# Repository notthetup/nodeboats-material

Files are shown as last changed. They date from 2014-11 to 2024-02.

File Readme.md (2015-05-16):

# NodeBoats Workshop


## Workshop Material

- [What to bring along?](instructions.md)
- [Workshop Introduction](presentation.md)
- [Getting Started](getting-started.md)
- [Ideas/Inspiration](ideas.md)
- [Competition Information](competition.md)
- [What to do if there's no Internet](no-internet.md)

### Aim

Let's Make something! Inspired by [NodeBoats at JSConf](http://makezine.com/2014/06/02/turning-coders-into-makers-at-jsconf-2014/)

Let's build boats that can be controlled by web technologies. We will make boats that can communicate over WiFi to a Node app.

The exact design of the boat and the control will be up to the individual team's creativity.

### Teams

- Maximum of 10 teams (that's all the kits we have)
- Each team has 2 members

### CampJS V 2015

**NodeBoats workshop at [CampJS V](http://v.campjs.com/)**

**Date** : 23-24th May 2015

**Venue** : Beach, Lord Somers Camp, Victoria, Australia

**Time** : 10am - 5pm *Catch the race on Sunday at TBA!*

### Competition

We will have a competition at the end of the day using the boats everyone created. The exact goal of the competition will be announced during the workshop.

The competition will be held at the **Beach at 5pm**

There will be prizes!

### Links

### History

*This workshop was first carried out at [JS Conf Asia 2014](http://2014.jsconf.asia/). Checkout the [Nodeboats Workshop Gallery](https://www.facebook.com/media/set/?set=a.615900415180712.1073741830.224477610989663&type=1).*

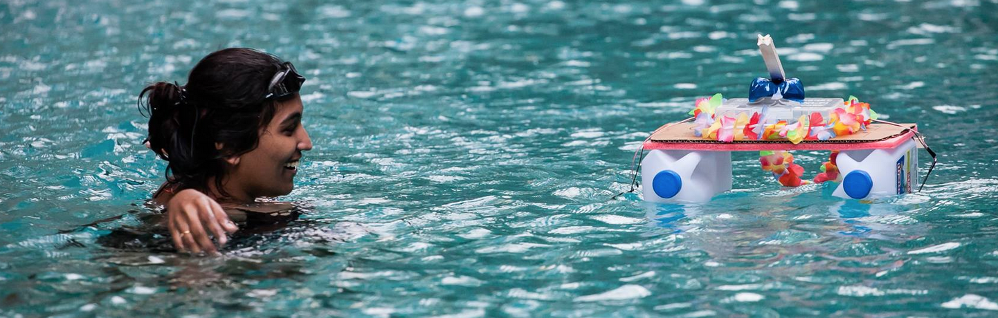
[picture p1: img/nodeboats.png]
Nodeboats workshop gallery (https://www.facebook.com/media/set/?set=a.615900415180712.1073741830.224477610989663&type=1)


#### JS Conf Asia 2014

**Nodeboat Builder workshop at [JSConf.Asia 2014](http://2014.jsconf.asia/)**

**Date** : 20th November 2014

**Venue** : Amara Sanctuary, Sentosa, Singapore

**Time** : 9.15am - 5:30pm *Catch the race at 5:15pm!*

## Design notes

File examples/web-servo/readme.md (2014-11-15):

#Rotate servo from the web

Using:

1. [Express](http://expressjs.com/)
- [Spark io](https://www.spark.io/)
- [Johnny Five](https://github.com/rwaldron/johnny-five)

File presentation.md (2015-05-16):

# NodeBoats Workshop!

# Material can be found in this github repo

**[bit.ly/nodeboatsworkshop](http://bit.ly/nodeboatsworkshop)**

# Grab your Kits
 - SparkCore Maker Kit
 - 1 Tamiya Submarine Motor
 - 1 Battery holder
 - 1 Pack of battries

# Hardware

We have a bunch of hardware, extra motors, tools and stuff. Help yourself, but don't be greedy!

# Get started with your Spark Core

- [Follow instructions here](getting-started.md)

# Get ready for the competition!

- [Competition information here](competition.md)
- Remember we're all here to share our <3 for JS and learn with each other. The competition is just for lulz.

# Let's work together and make some fricking robots!

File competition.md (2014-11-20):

# Competition.

## Time and Location

The competition will be held at the Dream Pool at Amara Sanctuary, at 5.15pm on 20th November 2014.

## Rules

1. All boats have to be controlled using remote control.
2. The boats have to complete the stipulated path as quickly as they can.
3. Any boat that sinks or drops something into (pollutes) the water will be disqualified.

## Competition Path

- Aim : Cross the dreamspool.
- Start : The wall nearest to the JSConf venue.
- End : The wall furthest from the JSConf venue.
- Metrics : How long you take to cross. Fastest wins!
- Tip : The waterfall on the side causes a constant water current towards the left.
- If your boat gets stuck or looses connection, we'll retrieve it for you and start over.

## Time Slots

1. Red Martians
2. The Sinking Barge
3. Superhero
4. RedMart Shark Boat
5. The JLT pearl
6. Cthulu
7. MeijiJS
8. Joosh Boat
9. NodeShip
10. Milky Way
11. Astuti

## Judging Criteria

| Criteria | Percentage | Notes |
| --- | --- | --- |
| Boat Design | 33.3333% | |
| Controller Design | 33.3333% | |
| Speed | 33.3333% | _Vrooooommm_ |
| Coin Toss | 0.0001% | _for Math_ |

## Prizes

1. [Hexy](http://arcbotics.com/products/hexy/)
2. [Sparki](http://arcbotics.com/products/sparki/)
3. [Raspberry Pi + Sparkfun Robot Board](https://www.sparkfun.com/products/11561)

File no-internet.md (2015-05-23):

# NodeBoats without Internet access

The current NodeBoats design uses [Spark Cloud](http://docs.particle.io/core/api/) to know the IP Address of the Spark Core. This IP Address is then used to communicate with the Spark Core.

So while, technically all the control communication happens locally, the initial step needs internet access.

In case of situations where internet access is flaky or inexistant, [MDNS](http://en.wikipedia.org/wiki/Multicast_DNS) can be used to exchange the IP Address based on a __HostName__.

## Setting up the SparkCore for MDNS

### Notes

- Unfortunately, the SparkCore tends to be flaky without a good connection to the SparkCloud, and can end trying to connect and not accepting any TCP messages.

- However, the Spark Core has a __SEMI_AUTOMATIC__ mode which allows it to run without a connection to Spark Cloud.

- Running the Spark Core in the __SEMI_AUTOMATIC__ will means none of the Spark APIs are accessible on the Spark Core or vice-versa.

- Hence, using the MDNS version of the SparkCore firmware, you won't be able to use the original version of `spark-io` or Spark APIs.

- You will have to __turn off your firewall__ to allow MDNS to work.

### Steps

1. Open the [Particle Build IDE](https://build.particle.io/build/#code).
2. Create a new App.
3. Copy and paste the firmware code from the [MDNS version of VoodooSpark](https://github.com/notthetup/voodoospark/blob/master/firmware/voodoospark.cpp) into the Build IDE.
4. Change the `CoreUID` to a unqiue string.
	```
	#define CoreUID "myPirateShip"
	```
5. Open the [Libraries Tab](https://build.particle.io/build/#libraries) in the Build IDE.
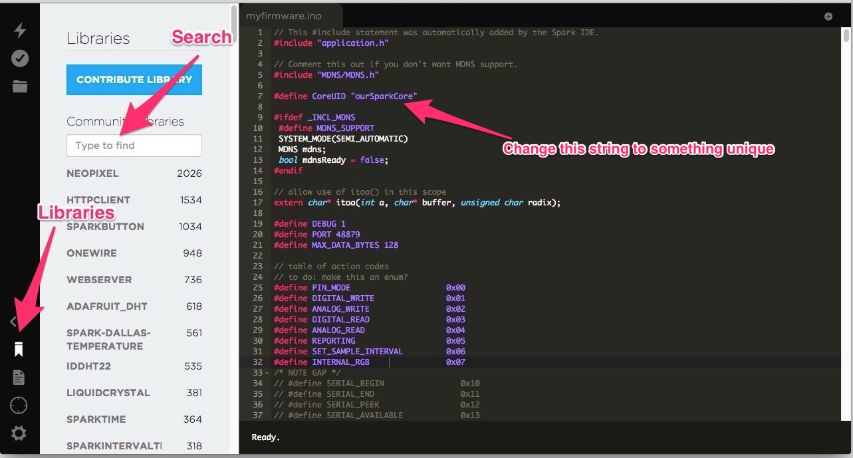
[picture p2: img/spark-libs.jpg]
spark libraries
	
6. Search for the [MDNS library](https://github.com/mrhornsby/spark-core-mdns).
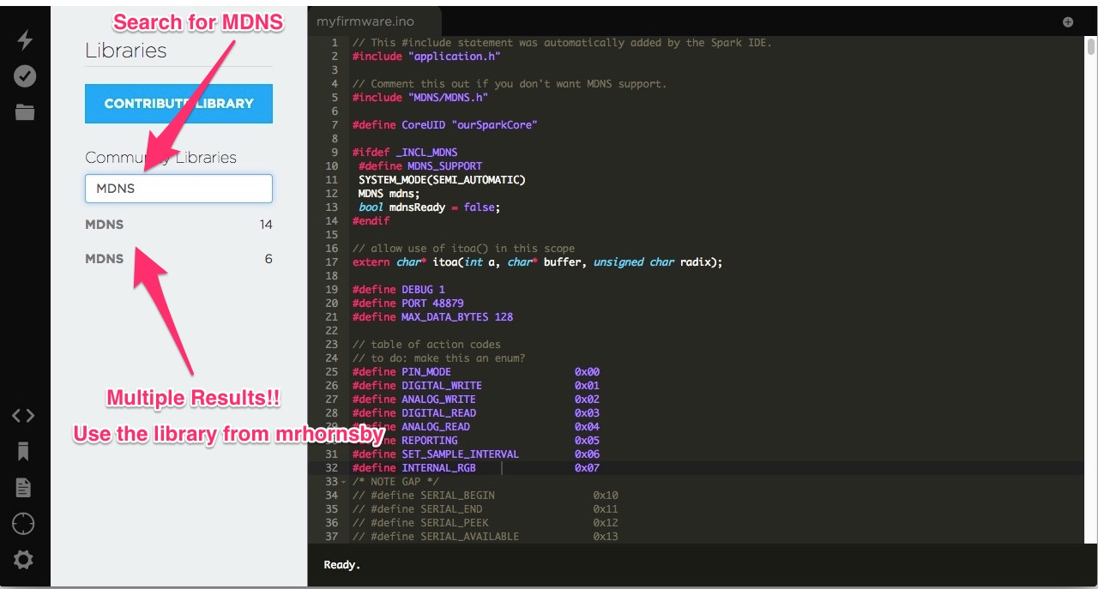
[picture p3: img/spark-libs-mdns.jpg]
spark libraries
	
7. Add the MDNS library to your new App.
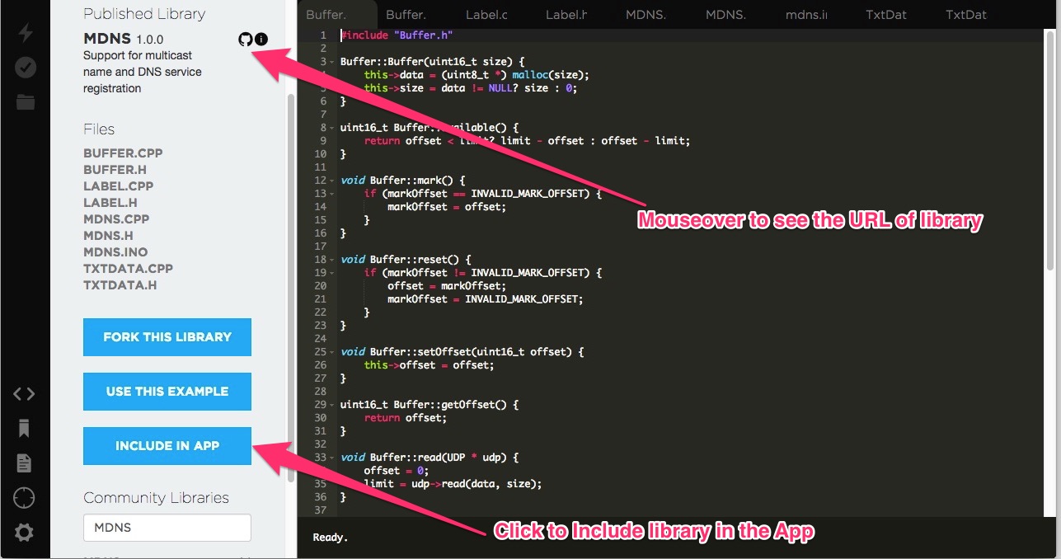
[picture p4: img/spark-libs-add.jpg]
spark libraries
	
8. Flash the new Firmware onto your SparkCore.

## Setting up the Spark-io for MDNS

- This [fork of Spark-io](https://github.com/notthetup/spark-io) supports MDNS.
- You might have to remove the original version of `spark-io`.
- You can install this using npm and the git url

	```shell
	npm i notthetup/spark-io
	```
- The MDNS version of `spark-io` works exactly the same, but tries to look for MDNS messages if a parameter called `hostname` is passed to the option Object in the constructor of `Spark`.

	```js
	var board = new five.Board({
	io: new Spark({
		hostname:'myPirateShip',
		deviceId:'{DEVICE_ID}',
		token:'{ACCESS_TOKEN}'
	})
});
	```

## Restoring Spark Core to original firmware.

### Notes

- Since the MDNS version of the firmware doesn't connect to Spark Cloud, re-flashing from the [Build IDE](https://build.particle.io/build/) will not work.
- To re-flash any other firmware, it easier to [first flash Tinker](https://github.com/spark/particle-cli#flashing-a-known-app) using dfu mode and then flash a new Firmware from the [Build IDE](https://build.particle.io/build/).

### Steps

1. Connect the Spark Core to USB.
2. Put the Spark Core in [dfu mode](http://docs.particle.io/core/modes/#core-modes-dfu-mode-device-firmware-upgrade).
3. Flash in Tinker using the `particle-cli` command

	```shell
	particle flash --usb tinker
	```
4. Wait for the Spark Core to be breathing cyan again before using it normally.

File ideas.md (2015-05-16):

# NodeBoats Twitter

[@nodeboats](https://twitter.com/nodeboats)

# NodeBoats at JSConf US

[Turning Coders into Makers](http://makezine.com/2014/06/02/turning-coders-into-makers-at-jsconf-2014/)

## Videos from JSCon US

[NodeBoats at JSConf 2014](https://www.youtube.com/watch?v=247MTokODOA)

[NodeBoats at JSConf2014](https://www.youtube.com/watch?v=eKqwo-jvRYo)

[Little ship nodeboat](https://www.youtube.com/watch?v=Kn9UaVDxHW8)

[Big nodeboat destroyer pirate ship](https://www.youtube.com/watch?v=zC0doS9-XZk)

[Look Ma! No Hands!](http://instagram.com/p/vXDkZywojq/)

## Videos from JSConf Asia

[NodeBoats at JSConf Asia 2014](https://www.youtube.com/watch?v=enCPdL7UnMw)

[NodeBoats Test](https://www.youtube.com/watch?v=YeJFM1E-l0o)

## Videos from RobotsConf

[NodeBoats Disaster!](https://www.youtube.com/watch?v=sJV63CuJXhQ)

[NodeBoat PaddleBoat Design](https://www.youtube.com/watch?t=10&v=A5_zRe0FQhk)

# Boat Design Ideas

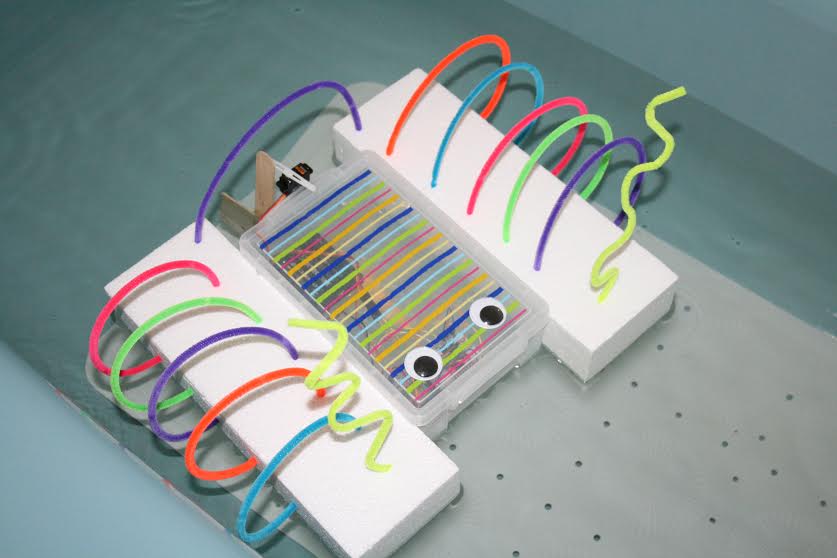
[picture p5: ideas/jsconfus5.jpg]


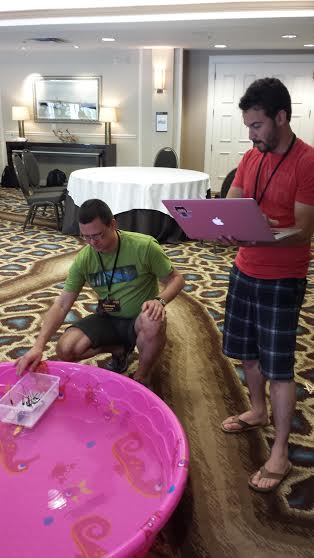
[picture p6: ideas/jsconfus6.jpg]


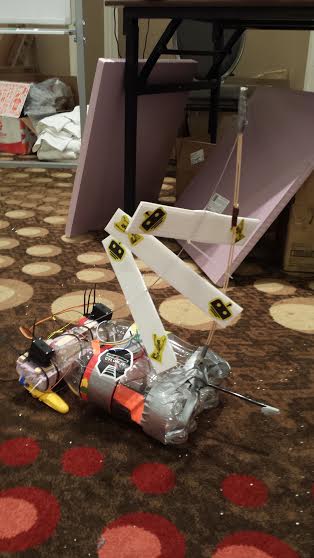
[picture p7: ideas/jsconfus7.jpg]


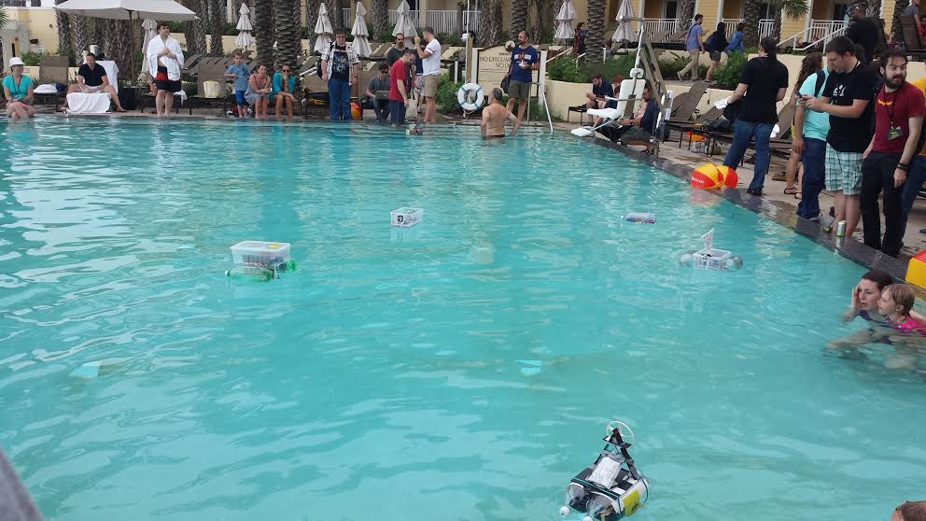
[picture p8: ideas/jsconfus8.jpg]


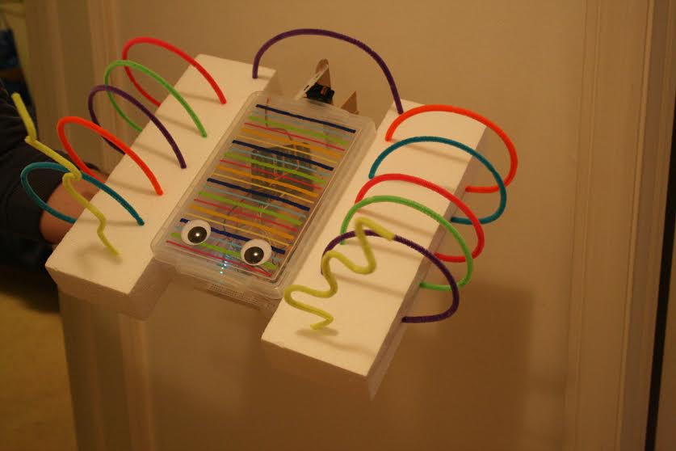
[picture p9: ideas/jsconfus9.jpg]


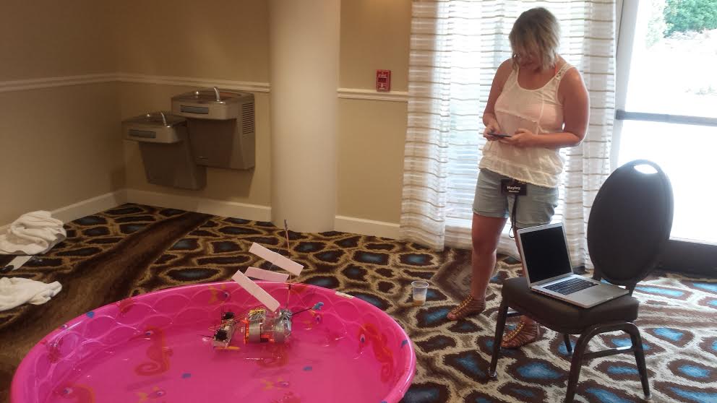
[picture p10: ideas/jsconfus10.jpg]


# Hacking the Tamiya Submarine Motor

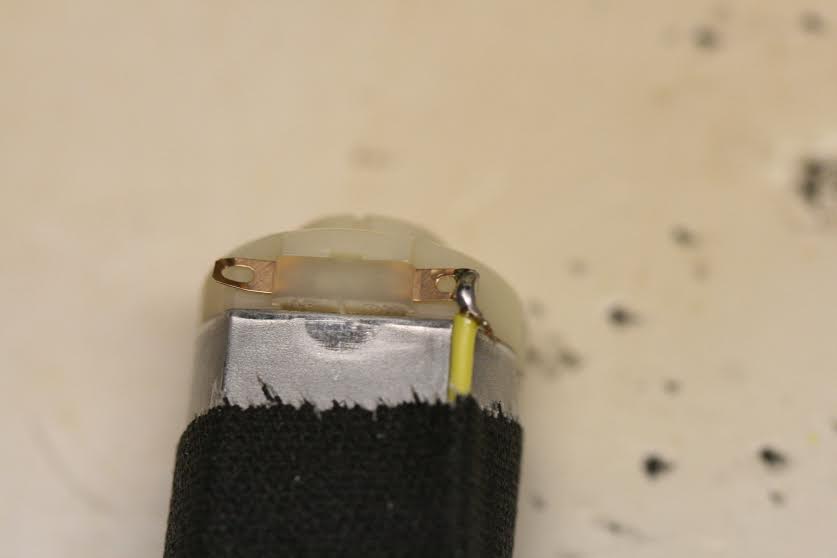
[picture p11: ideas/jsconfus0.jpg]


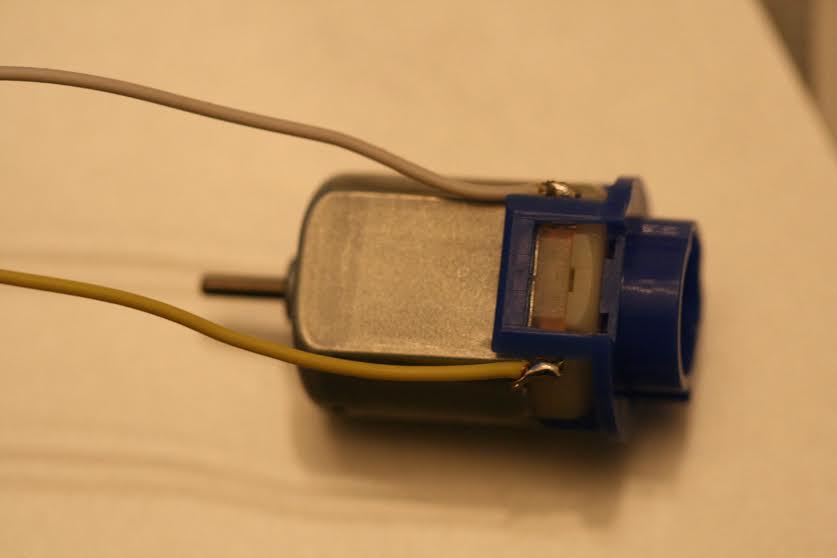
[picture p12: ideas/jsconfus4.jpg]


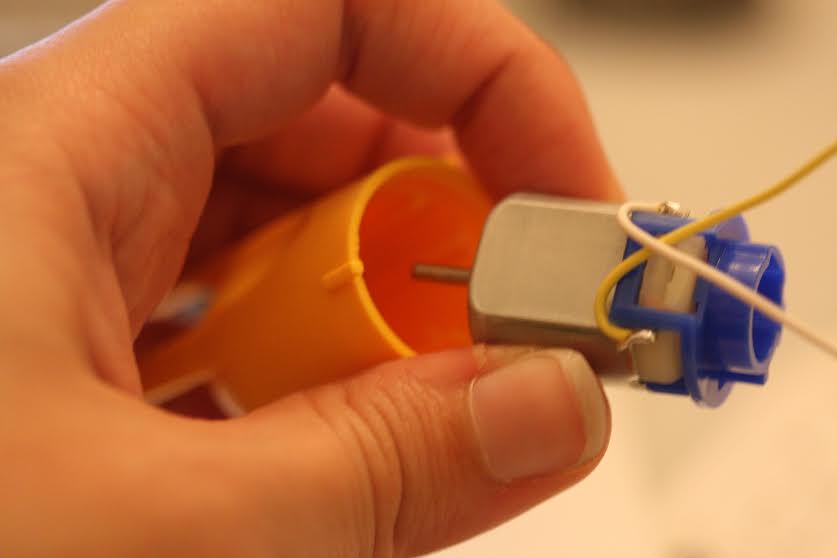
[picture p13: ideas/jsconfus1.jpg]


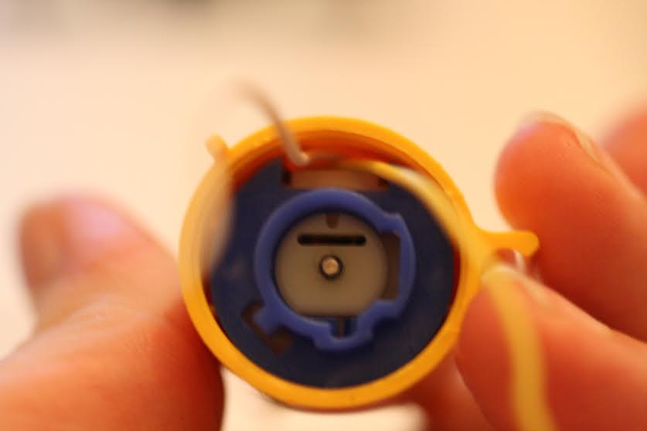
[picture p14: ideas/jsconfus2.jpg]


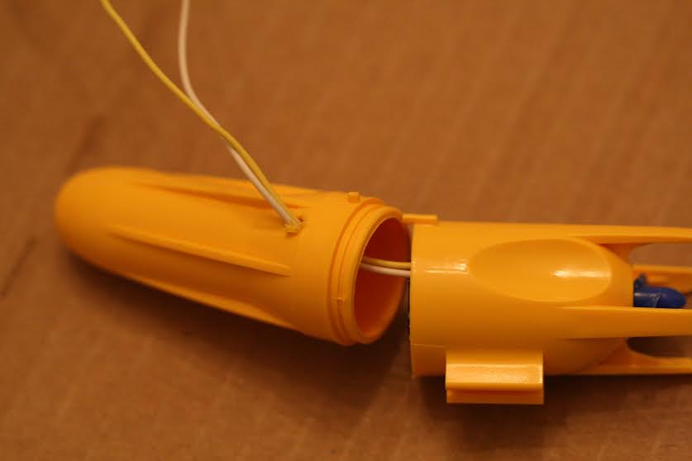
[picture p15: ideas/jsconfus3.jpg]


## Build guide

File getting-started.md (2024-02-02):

# Chapter 1 - Spark Core

# #Step 1: Setup

### Note : Spark has officially [changed their name to Particle](http://blog.particle.io/2015/05/13/spark-is-now-particle/). While most of the URLs here should work, if something doesn't work. Please try replacing 'Spark' with 'Particle'.

#### Aim: Turn on and off the `D7` LED on Spark Core from the particle-cli

1. **Create a Spark Core account and claim your spark**

	1. Go to the [Spark Core website](https://www.particle.io/)
	- Click `Build` to create an account
- Glance through the [documentation](http://docs.particle.io/core/api/)
	- Blinking [LED colors/actions and their meanings](http://docs.particle.io/core/#step-3-connect-your-core-to-the-cloud)
	- Spark Core [pinout diagram](http://docs.particle.io/assets/images/spark-pinout.png)
- **Connect the Spark Core**
	1.  Go through the steps in the [starting docs](http://docs.particle.io/core/)
	- Plug the micro USB of the Spark Core to your laptop and see the blinking blue light
- **Claim your Spark Core using particles-cli**
	1. [Download and install particle-cli](https://www.npmjs.org/package/particle-cli) `npm install -g particle-cli`
	- [Setup particle-cli on your machine](http://docs.particle.io/core/cli/) with `particle setup`
	- Put your Spark Core into [listening mode](http://docs.particle.io/core/connect/#connecting-your-device-listening-mode).
	- Get your Spark's UID using `particle identify`

	```shell
		$ particle identify
		72398476273648244921384
	```
	- Claim your Spark Core using the command `particle device add {SPARK_UID}`

	```shell
		$ particle device add 72398476273648244921384
	```
	- Name your Spark Core using the command `particle core rename {SPARK_UID} {NAME}`

	```shell
		$ particle core rename 0123456789ABCDEFGHI "pirate frosting"
	```
	- Once your Spark Core is setup, the [LED on top it will start breathing cyan](img/breathing.gif)
	- [Control your SparkCore](http://docs.particle.io/core/cli/#blink-an-led-with-tinker) from `particle-cli` by turning on and off the LED connected to the "D7" pin

		```shell
		$ particle call {SPARK_CORE_NAME} digitalwrite D7,HIGH
		1
		$ particle call {SPARK_CORE_NAME} digitalwrite D7,LOW
		1
		```

	- We WILL NOT be using the Spark Mobile Apps to claim and configure the SparkCore to ensure that we don't have issues with which Spark Core you connect to.

## Step 2: Curl

#### Aim: Turn on and off the `D7` LED with HTTP via curl commands

1. Now that we can control the Spark Core with code, we need to be able to do it wirelessly. SparkCore has a built-in WiFi module (that we configured earlier) that allows us to talk to it over HTTP. Let's see how that works.
- If you forget your `Device ID` and `Access Token` you can also get it from the Spark Website.
	1. Get your `Device ID` from [here](https://build.particle.io/build#cores) and click on `Core`
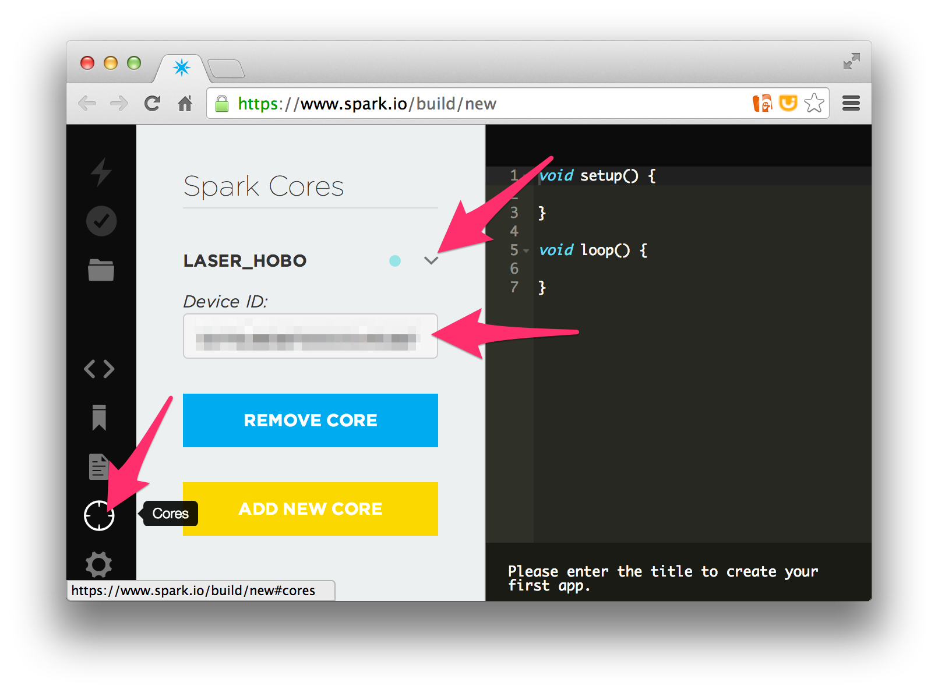
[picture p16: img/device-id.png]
		
	- Get your `Access Token` from [here](https://build.particle.io/build#cores) and click on `Settings`
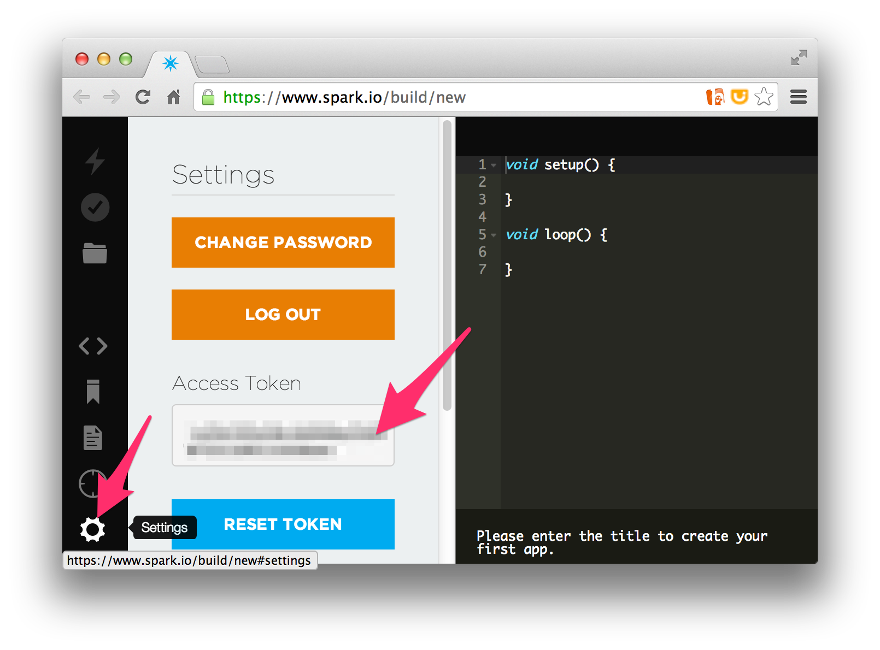
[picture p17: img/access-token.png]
		
- Connect to your Spark Core from your laptop's command line with a HTTP GET request using the Spark Cloud API. Note the 4 exposed functions "digitalread", "digitalwrite", "analogread" and "analogwrite"
  ```shell
  $ curl -X GET -H "Authorization: Bearer {ACCESS_TOKEN}" https://api.particle.io/v1/devices/{DEVICE_ID}

  {
    "id": "{DEVICE_ID}",
    "name": "{DEVICE_NAME}",
    "connected": true,
    "variables": {},
    "functions": [
      "digitalread",
      "digitalwrite",
      "analogread",
      "analogwrite"
    ]
  }
  ```
- Now, turn on and off the `D7` LED with Spark Cloud API using the HTTP POST request to the `digitalwrite` endpoint

	1. Turn on the LED with params `D7,HIGH`

	  ```shell
	  curl -X POST -H "Authorization: Bearer {ACCESS_TOKEN}" https://api.particle.io/v1/devices/{DEVICE_ID}/digitalwrite -d params=D7,HIGH

	  {
	    "id": "{DEVICE_ID}",
	    "name": "{DEVICE_NAME}",
	    "last_app": null,
	    "connected": true,
	    "return_value": 1
	  }
	  ```
	- Turn off the LED with params `D7,LOW`

	  ```shell
	  curl -X POST -H "Authorization: Bearer {ACCESS_TOKEN}" https://api.particle.io/v1/devices/{DEVICE_ID}/digitalwrite -d params=D7,HIGH

	  {
	    "id": "{DEVICE_ID}",
	    "name": "{DEVICE_NAME}",
	    "last_app": null,
	    "connected": true,
	    "return_value": 1
	  }
	  ```

## Step 3: Setup with Node.js

#### Aim: Turn on and off the `D7` LED over TCP.

1. While using Spark Cloud and HTTP is a great way of controlling the Spark Core wirelessly, we need something a with a lot less latency. So we have to ditch HTTP to go with pure TCP.
- [voodoospark](https://github.com/voodootikigod/voodoospark) is a great firmware for the SparkCore which listens to packets over TCP. It implements a RPC style binary protocol which can do basic functions like turning on/off specific pins on the Spark. Just what we need.
- **Load the firmware**
	1. The latest version (> 2.5.0) of the voodoospark firmware is [bundled together with particle-cli as a binary](https://github.com/spark/particle-cli/tree/master/binaries).
	- particle-cli[ provides a handy way of flashing voodoospark](https://github.com/spark/particle-cli#flashing-a-known-app) (or reset the Spark Core to the original Tinker firmware) using the command :
	```shell
		$ particle flash {DEVICE_ID} voodoo
	```
	- Wait for the core to start breathing cyan.
	- Run the curl command again and see what functions are exposed now

		```shell
		$ curl -X GET -H "Authorization: Bearer {ACCESS_TOKEN}" https://api.particle.io/v1/devices/{DEVICE_ID}

		{
		  "id": "{DEVICE_ID}",
		  "name": "{DEVICE_NAME}",
		  "connected": true,
		  "variables": {
		    "endpoint": "string"
		  },
		  "functions": [],
		  "cc3000_patch_version": "1.29"
		}
		```
	- Check the local IP address of the Spark Core. `result` will give you the IP.

		```shell
		$ curl -X GET -H "Authorization: Bearer {ACCESS_TOKEN}" https://api.particle.io/v1/devices/{DEVICE_ID}/endpoint

		{
		  "cmd": "VarReturn",
		  "name": "endpoint",
		  "result": "{LOCAL_IP_ADDRESS}",
		  "coreInfo": {
		    "last_app": "",
		    "last_heard": "{CURRENT DATETIME}",
		    "connected": true,
		    "deviceID": "{DEVICE_ID}"
		  }
		}

		```
- **Create blinking LED with Node**
	1. Spark-io is the companion JS library which can speak the same binary RPC protocol over TCP as the voodoospark does. Let's install that!
	- Install Spark-io with `npm install spark-io`
	- [Store the `Device ID` and `Access Token`](https://github.com/rwaldron/spark-io#getting-started) in a `~/.sparkrc` file
	- Create a [blinking LED node script](https://github.com/rwaldron/spark-io#blink-an-led)
	- Create the [blinking LED with Johnny Five plugin](https://github.com/rwaldron/spark-io#johnny-five-io-plugin)
	- Create another node script. When you run this the [node repl](http://nodejs.org/api/repl.html) will appear

		```js
		var five = require("johnny-five");
		var Spark = require("spark-io");

		var board = new five.Board({
		  io: new Spark({
		    token: process.env.SPARK_TOKEN,
		    deviceId: process.env.SPARK_DEVICE_ID
		  })
		});

		board.on("ready", function() {
		  var led = new five.Led("D7");

		  // This bit of js injects the led variable into the
		  // repl you get after this script finishes execution.
		  board.repl.inject({
		    led: led
		  });

		});
		```
		Turn on / off the LED in the repl with these commands:
		- `>> led.on()`
		- `>> led.off()`

		Blink / stop the LED in the repl with these commands:
		- `>> led.blink()`
		- `>> led.stop()`

# Chapter 2 - Motors & Servo

Now that we have the SparkCore under our almost realtime control, lets figure out how we can use it to control motors. Motors are awesome as they make things move!

We will be needing a few common electronics components for this part of the workshop. Let's briefly look at what we may need.

## Step 1: Know the components

<table style="vertical-slign:top;">
	<tr>
		<td width="4%">#</td>
		<td width="32%">Name & Notes</td>
		<td width="32%">Schematic</td>
		<td width="32%">Photo</td>
	</tr>
	<tr>
		<td>1</td>
		<td>
			<strong>Breadboard</strong>
			<ul>
				<li><a href="http://en.wikipedia.org/wiki/Breadboard">Wikipedia</a></li>
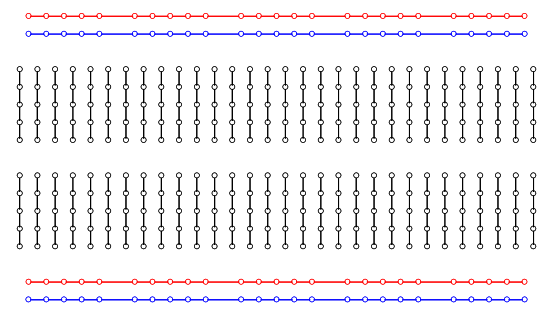
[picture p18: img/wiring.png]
				<li>Wiring pattern in a breadboard<br></li>
				<li>
					<strong>Horizontal rows</strong>
					<ul>
						<li>HIGH / Vin (~6V)</li>
						<li>LOW / Gnd (0V)</li>
					</ul>
				</li>
				<li><strong>Tip: </strong> Plug in the +/- of the batteries to the horizontal rows and connect +/- ends from any components on the breadboard to these lines.</li>
			</ul>
		</td>
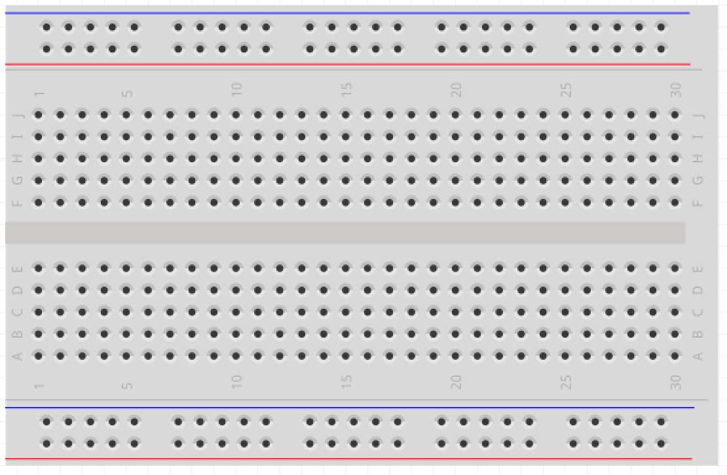
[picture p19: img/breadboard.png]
		<td></td>
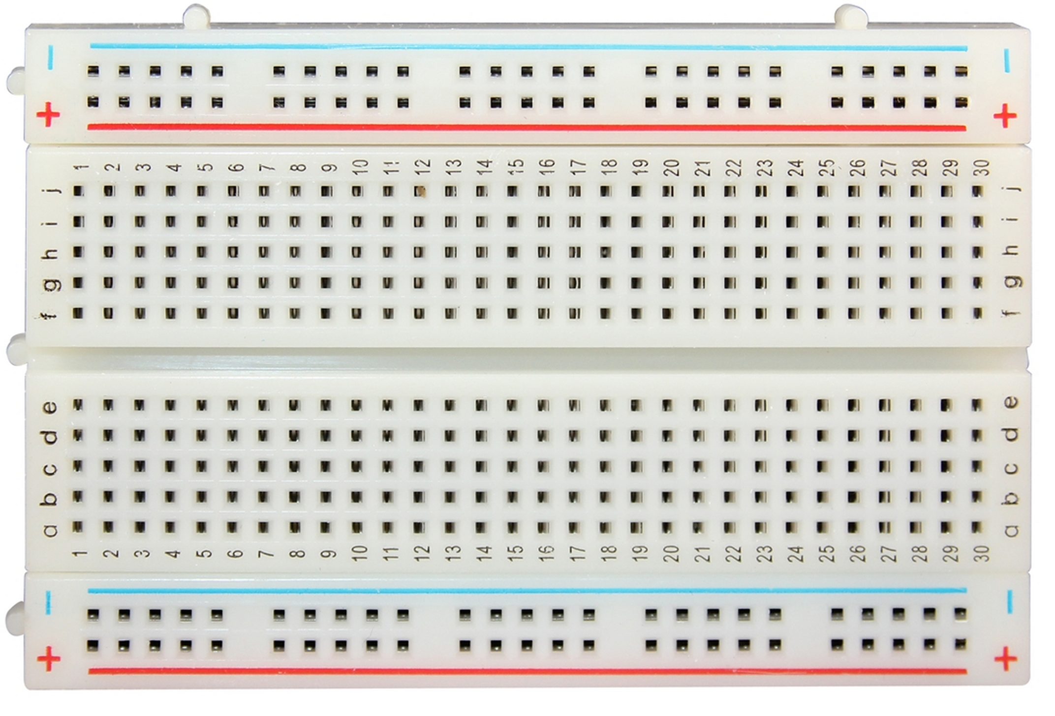
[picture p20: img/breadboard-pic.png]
		<td></td>
	</tr>
	<tr>
		<td>2</td>
		<td>
			<strong>Spark Core</strong>
			<ul>
				<li><a href="http://docs.particle.io/assets/images/spark-pinout.png">pinout diagram</a></li>
				<li><a href="http://docs.particle.io/start/#step-3-connect-your-core-to-the-cloud">LED colors/actions and their meanings</a></li>
			</ul>
		</td>
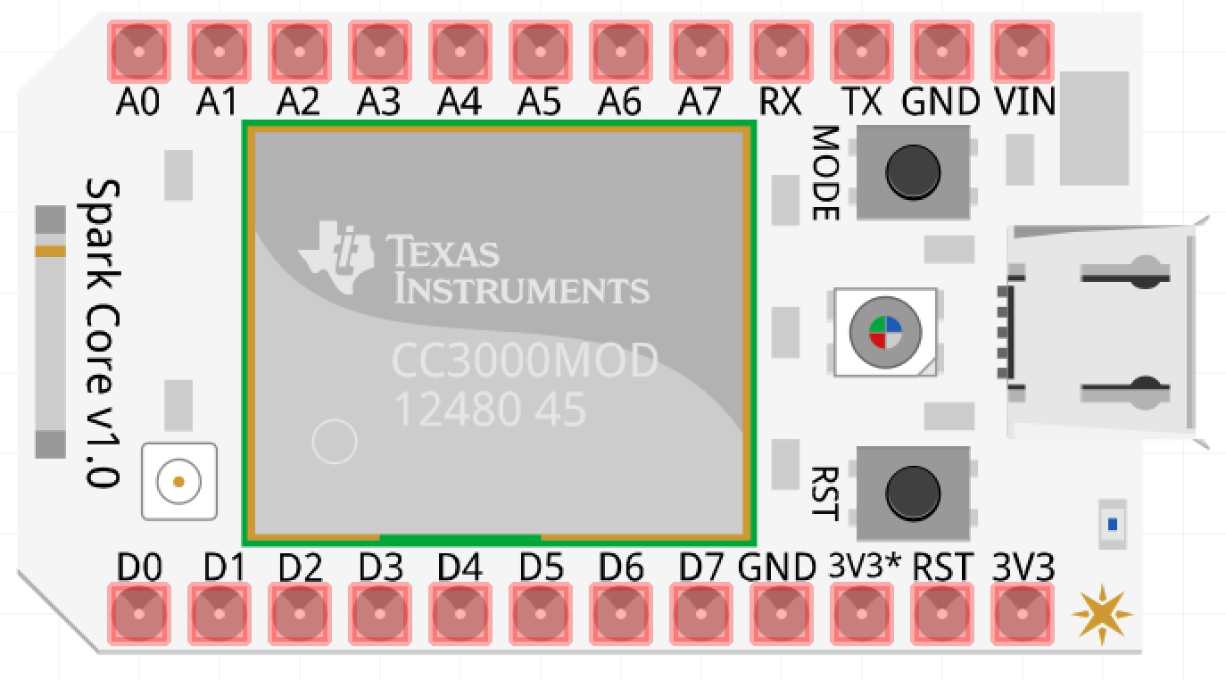
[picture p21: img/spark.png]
		<td></td>
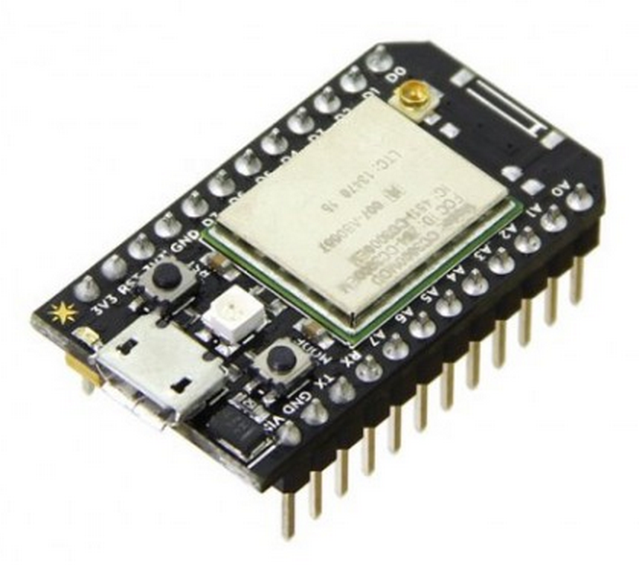
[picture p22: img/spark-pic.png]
		<td></td>
	</tr>
	<tr>
		<td>3</td>
		<td>
			<strong>Motor Driver chip L293NE</strong>
			<ul>
			 	<li><a href="http://www.ti.com/lit/ds/symlink/l293d.pdf">datasheet</a></li>
			 	<li><strong>Tip:</strong> Note the position of the notch on the schematic and place this chip on the breadboard accordingly. It will help to point out the pin positions for debugging and wiring.</li>
		 	</ul>
		 </td>
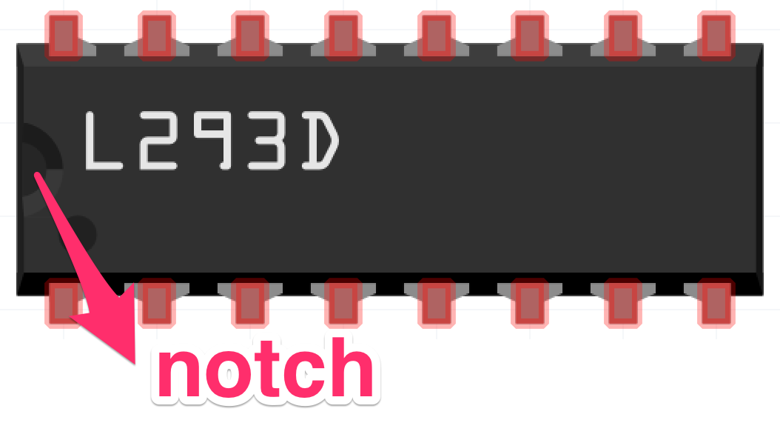
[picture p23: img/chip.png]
		<td></td>
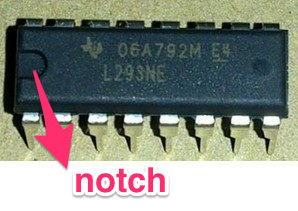
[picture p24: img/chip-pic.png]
		<td></td>
	</tr>
	<tr>
		<td>4</td>
		<td>
			<strong>Diode</strong>
			<ul>
				<li><a href="http://en.wikipedia.org/wiki/Diode">Wikipedia</a></li>
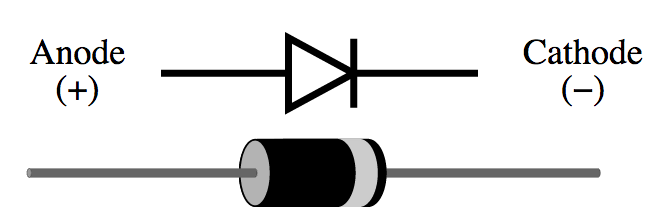
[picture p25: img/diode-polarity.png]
				<li>diode polarity<br></li>
				<li>
					In this case, the diodes are used for inductive transient suppression
					<br>
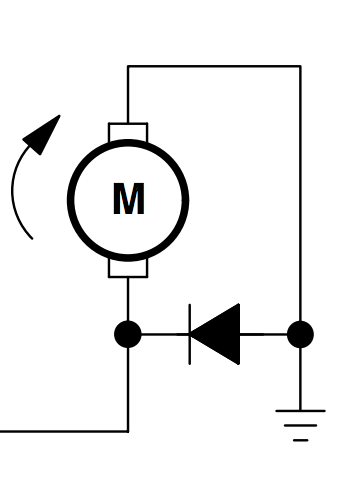
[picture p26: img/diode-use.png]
					
				</li>
				<li><strong>Tip: </strong> Note the white strip (cathode) of the diode while wiring up the breadboard. The anode is connected to the ground.</li>
			</ul>
		</td>
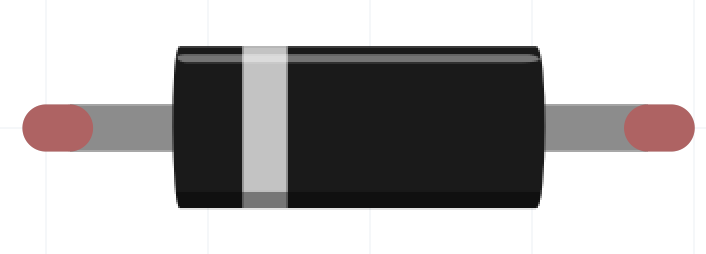
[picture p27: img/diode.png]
		<td></td>
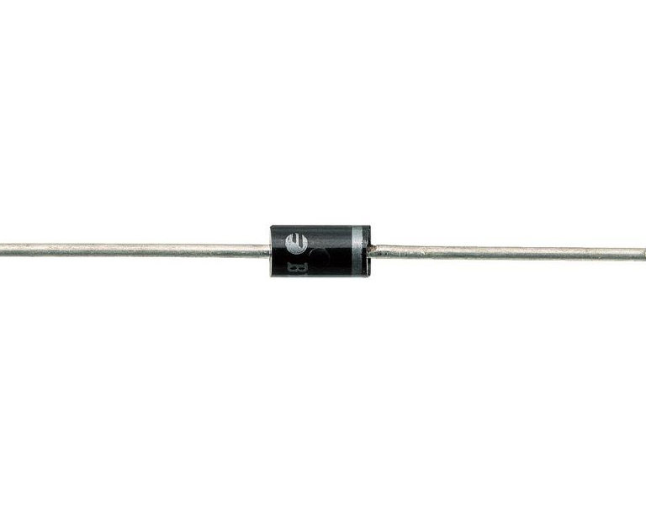
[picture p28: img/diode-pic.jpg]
		<td></td>
	</tr>
	<tr>
		<td>5</td>
		<td>
			<strong>LED</strong> (light emitting diode)
			<ul>
				<li><a href="http://en.wikipedia.org/wiki/Light-emitting_diode">Wikipedia</a></li>
				<li>
					LED polarity
					<ul>
						<li><strong>shorter leg: </strong>cathode - connect to ground</li>
						<li><strong>longer leg: </strong>anode - connect to power</li>
					</ul>
				</li>
				<li><strong>Tip: </strong>Instead of connecting to the motors/servo initially, use these LEDs for easier debugging.</li>
			</ul>
		</td>
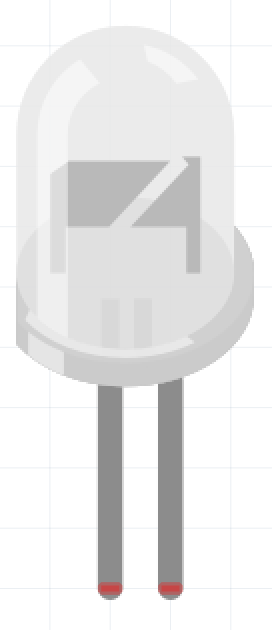
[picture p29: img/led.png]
		<td></td>
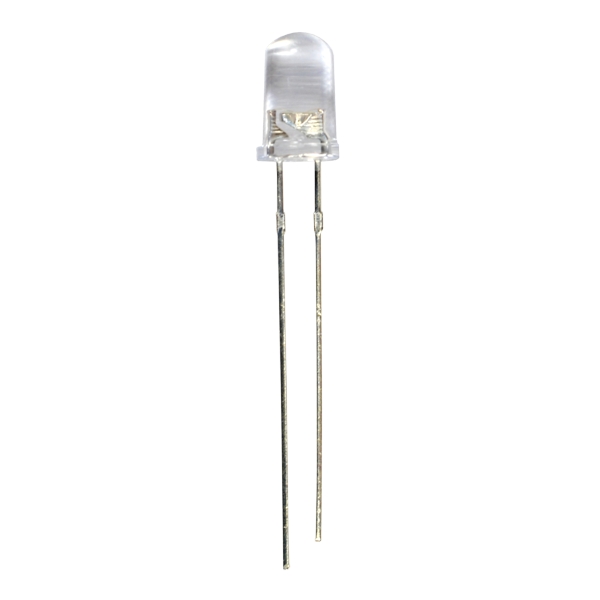
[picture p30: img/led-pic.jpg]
		<td></td>
	</tr>
	<tr>
		<td>6</td>
		<td>
			<strong>jumper cables</strong>
			<ul>
				<li><strong>Tip: </strong>Use the same color wires as the schematic so that it will be faster to trace the wires for debugging. E.g. use <strong>RED</strong> for power and <strong>BLACK</strong> for ground. <strong>YELLOW</strong> and <strong>GREEN</strong> for the motor endpoints.</li>
			</ul>
		</td>
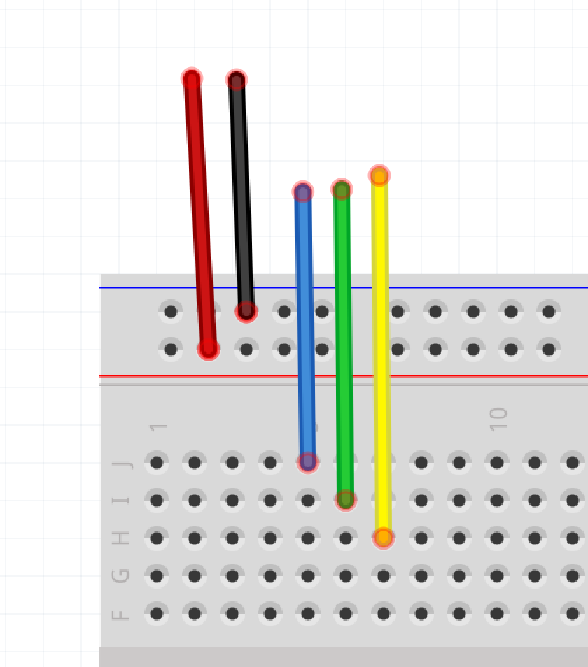
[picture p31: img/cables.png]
		<td></td>
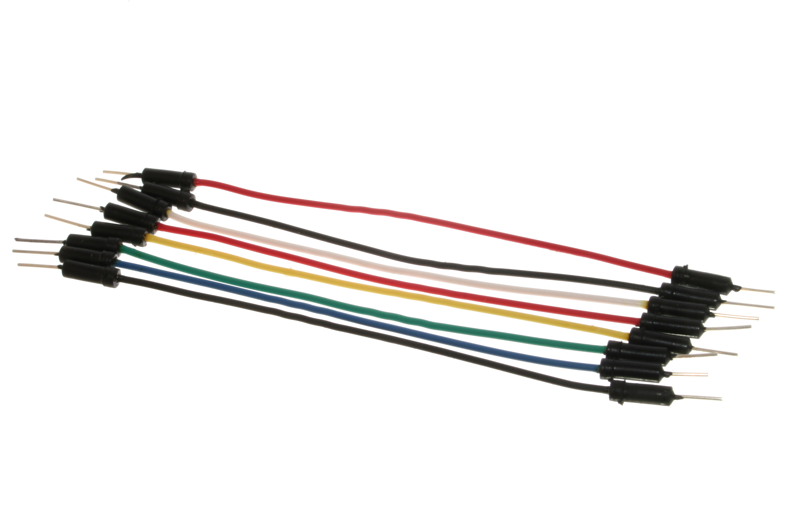
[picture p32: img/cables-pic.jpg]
		<td></td>
	</tr>
	<tr>
		<td>7</td>
		<td>
			<strong>battery pack</strong>
			<ul>
				<li>We will use 4 <a href="http://en.wikipedia.org/wiki/AA_battery">AA batteries</a> of 6V</li>
				<li><strong>Tip: </strong>Connect the +/- ends of the battery pack to the horizontal lines of the breadboard</li>
			</ul>
		</td>
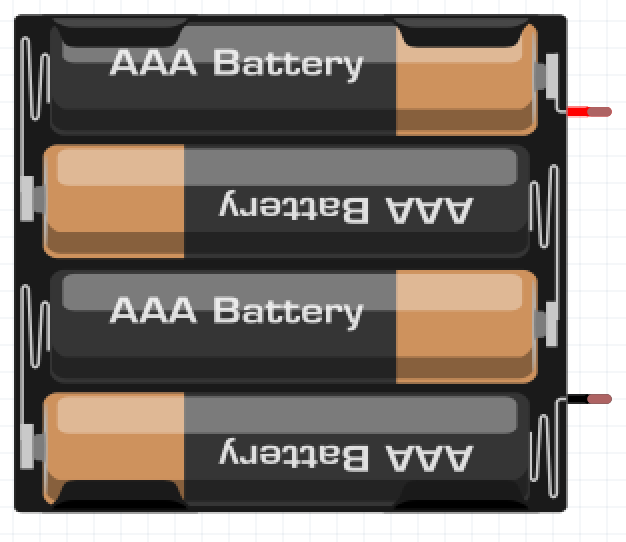
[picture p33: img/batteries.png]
		<td></td>
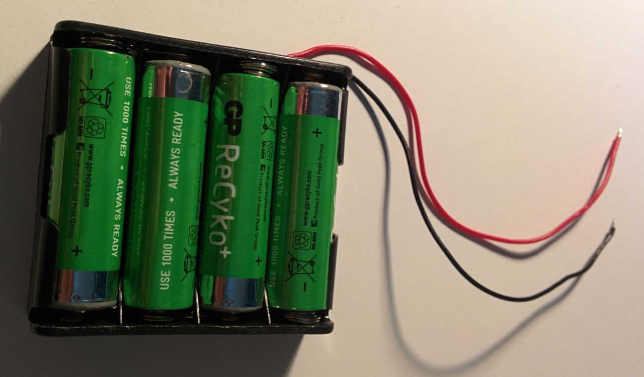
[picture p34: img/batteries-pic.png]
		<td></td>
	</tr>
	<tr>
		<td>8</td>
		<td>
			<strong>Motors</strong>
			<ul>
				<li><strong>Note: </strong>Motors don't have a Positive/Negative terminal. Depends on how they are attached they can either run forward or backward. </li>
				<li><strong>Tip: </strong>Use an LED to check for high and low before connecting the motors.</li>
			</ul>
		</td>
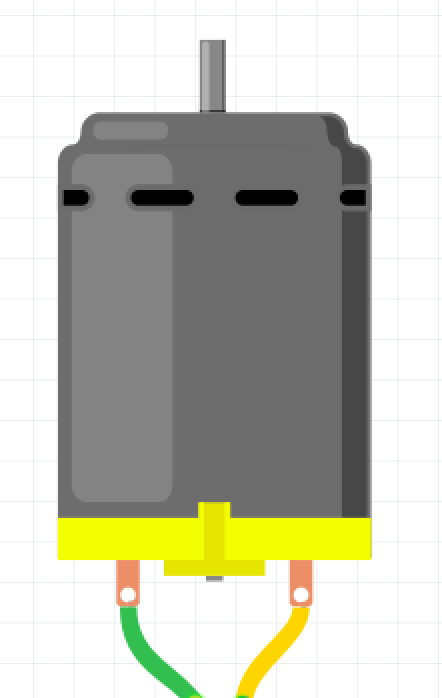
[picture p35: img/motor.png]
		<td></td>
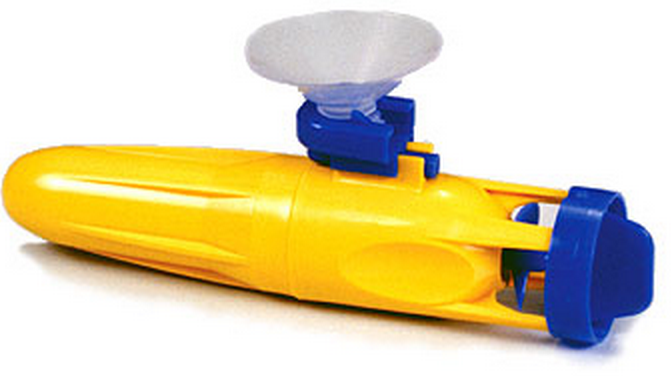
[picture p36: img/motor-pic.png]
		<td></td>
	</tr>
	<tr>
		<td>9</td>
		<td>
			<strong>Servo</strong>
			<ul>
				<li><a href="http://en.wikipedia.org/wiki/Servo_(radio_control)">Wikipedia</a></li>
				<li><a href="http://docs.particle.io/shields/#setting-up-the-shield-8-micro-servo-1">Spark and servo</a></li>
				<li><strong>Tip: </strong>For wiring - <em>Yellow</em> is Signal (D0, D1, A0, A1, A4, A5, A6, A7), <em>Orange</em> is +5V (VIN), <em>Brown</em> is ground</li>
			</ul>
		</td>
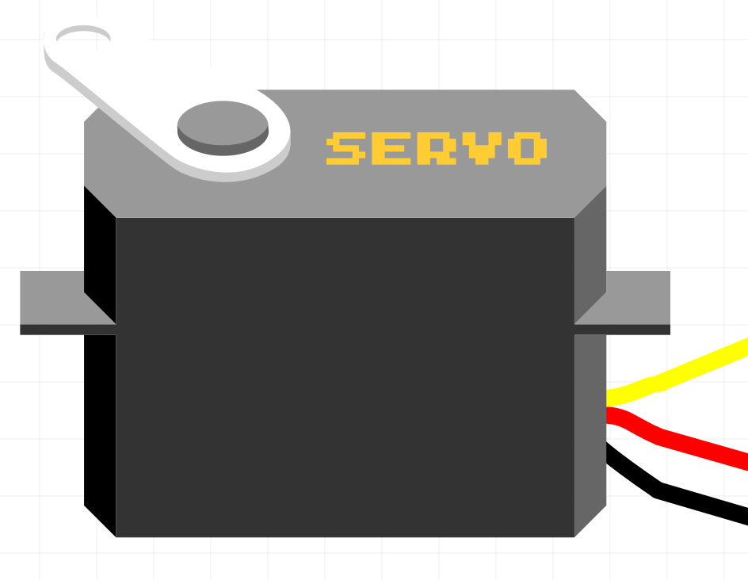
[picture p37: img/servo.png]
		<td></td>
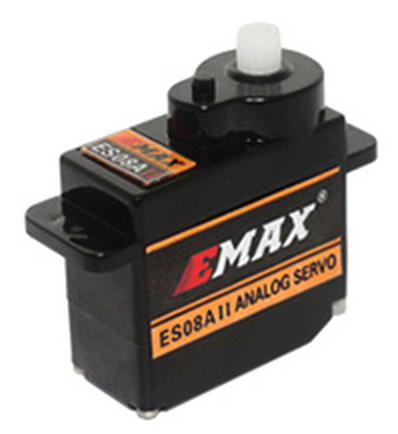
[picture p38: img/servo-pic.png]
		<td></td>
	</tr>
	<tr>
		<td>10</td>
		<td>
			<strong>Capacitor</strong>
			<ul>
				<li><a href="http://en.wikipedia.org/wiki/Capacitor">Wikipedia</a></li>
				<li><a href="http://docs.particle.io/shields/#setting-up-the-shield-2-electrolytic-capacitor-100uf-5">Capacitors</a></li>
				<li><strong>Tip: </strong> Capacitors have polarity. On the plastic above one of the pins you'll see a light coloured strip with a negative sign "-" on it. Always connect that pin to GND pins or rails </li>
			</ul>
		</td>
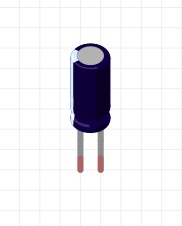
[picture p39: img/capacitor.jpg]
		<td></td>
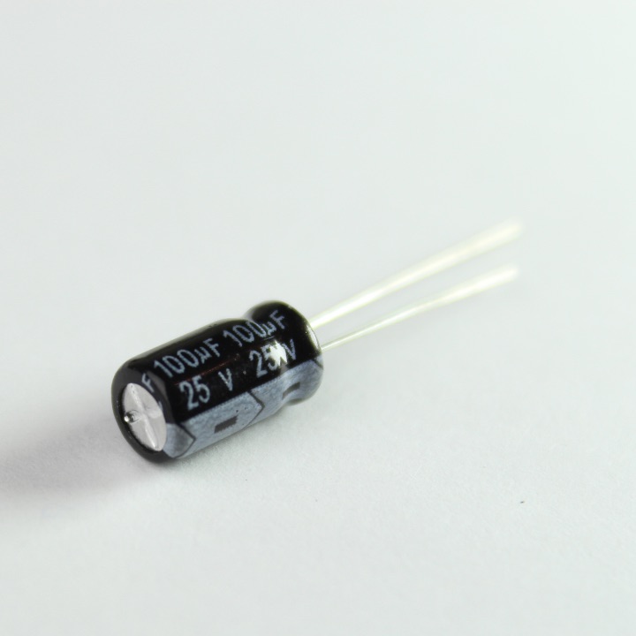
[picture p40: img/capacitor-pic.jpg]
		<td></td>
	</tr>
</table>

## Step 2: Wire up with an LED, then motor

To control a motor (propeller), we need to use a Motor Driver Integrated Chip (IC). This L293 IC is designed to allow microcontrollers like the Spark Core to control motors, which can draw lots of current.

The L293 Motor Driver is controlled using [Pulse Width Modulation](http://en.wikipedia.org/wiki/Pulse-width_modulation) from the SparkCore. This technique allows us to modulate the power provided to the L293 Motor Driver, and hence control the speed of the motor. Only a few pins on the SparkCore are able to output PWM signals (D0, D1, A0, A1, A4, A5, A6, A7).

For starters, lets wire up a L293 Motor Driver with LEDs instead of motors to check if our circuit works.

1. Follow the schematic below and wire it up accordingly with LEDs instead of
motors.
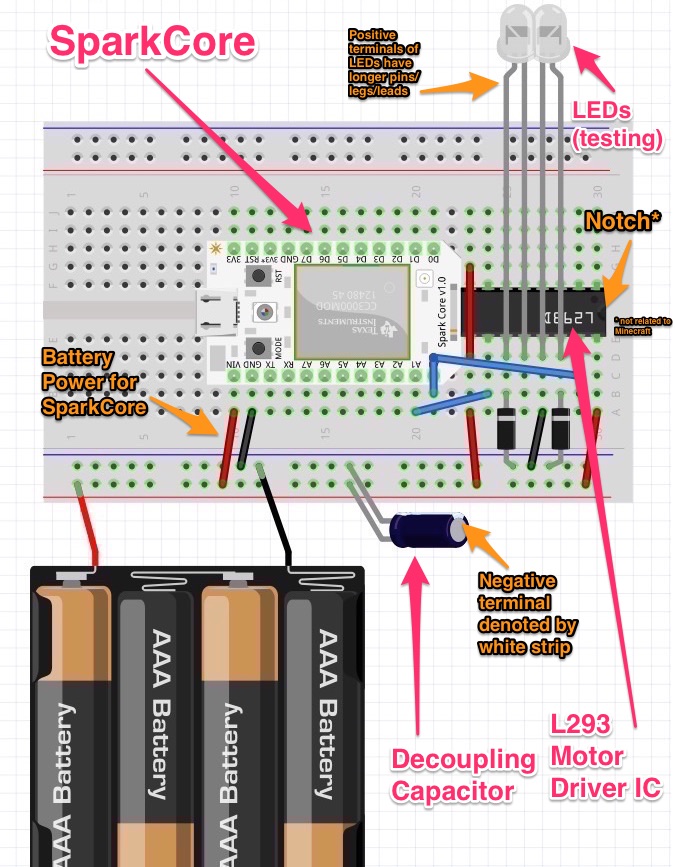
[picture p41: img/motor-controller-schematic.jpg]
Motor Controller with LED
	

	The original files for these schematic (made in [Fritzing](http://fritzing.org/download/)) are [here](https://github.com/notthetup/nodeboatbuilder/tree/master/schematics).

- The L293 Motor Driver IC pins are number as defined in this diagram

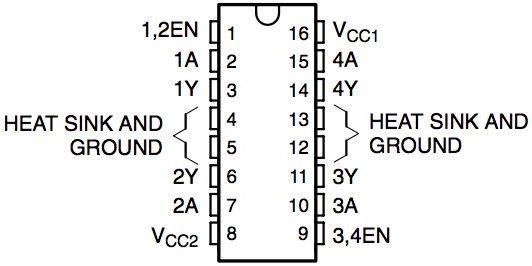
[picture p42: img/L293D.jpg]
	

- The connections you will be making are.

	| Signal         | Source                    | Destination  			       |
	|----------------|---------------------------|---------------------------|
	| Power(VCC)     | Battery Pack Red          | Power Rail on Breadboard  |
	| Ground(Gnd)    | Battery Pack Black        | Ground Rail on Breadboard |
	| Power(VCC)     | Vin on SparkCore          | Power Rail on Breadboard  |
	| Power(VCC)     | Pin 16 on L293D           | Power Rail on Breadboard  |
	| Power(VCC)     | Pin 8 on L293D            | Power Rail on Breadboard  |
	| Ground(Gnd)    | Gnd on SparkCore          | Ground Rail on Breadboard |
	| Ground(Gnd)    | Pin 12 on L293D           | Ground Rail on Breadboard |
	| Enable Motor   | Pin 9 on L293D            | Power Rail on Breadboard  |
	| Motor 1 Control| Pin A0 on SparkCore       | Pin 15 on L293D           |
	| Motor 2 Control| Pin A1 on SparkCore       | Pin 10 on L293D           |
	| LED 1 Positive | Pin 11 on L293D           | LED 1 Positive            |
	| LED 1 Negative | Pin 12 on L293D           | LED 1 Negative (shorter)  |
	| LED 2 Positive | Pin 14 on L293D           | LED 2 Positive            |
	| LED 2 Negative | Pin 13 on L293D           | LED 2 Negative (shorter)  |
	| Diode          | Ground Rail on Breadboard | Pin 11 on l293d           |
	| Diode          | Ground Rail on Breadboard | Pin 14 on L293D           |

- Create a file `motor.js` with the following code:

	```js
	var five = require("johnny-five");
	var Spark = require("spark-io");
	var board = new five.Board({
	  io: new Spark({
	    token: process.env.SPARK_TOKEN,
	    deviceId: process.env.SPARK_DEVICE_ID
	  })
	});

	board.on("ready", function() {
	  motorL = new five.Motor({
	    pin: 'A1'
	  });

	  motorR = new five.Motor({
	    pin: 'A0'
	  });

	  board.repl.inject({
	    l: motorL,
	    r: motorR
	  });

	});
	```
	Run this code with `node motor.js` - can you hear the motors running?

	```js
	>> r.start(50) // right LED should light up dim
	>> r.start(100) // right LED should light up bright
	>> r.stop() // right LED should not light up

	>> l.start(50) // left LED should light up dim
	>> l.start(100) // left LED should light up bright
	>> l.stop() // left LED should not light up
	```

## Hacking the Propeller

The Tamiya propeller is designed to be used with battries. We'll hack it to work with our motor controller. We have already drilled the propeller, you'll need to assemble the motor, the seal and the blade. Here are some steps. _There also are instructions on the paper that comes with the kit_

1. The Propeller Kit

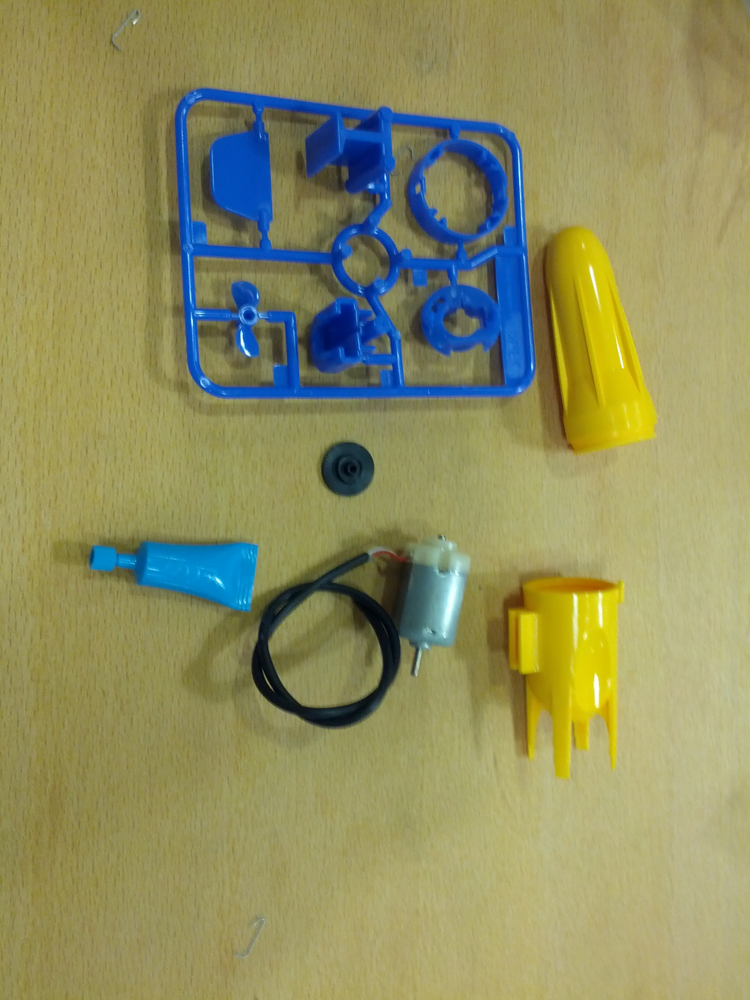
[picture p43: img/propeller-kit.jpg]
propeller kit
	

- Add the Blue Plastic bracket on the motor. _Click!_

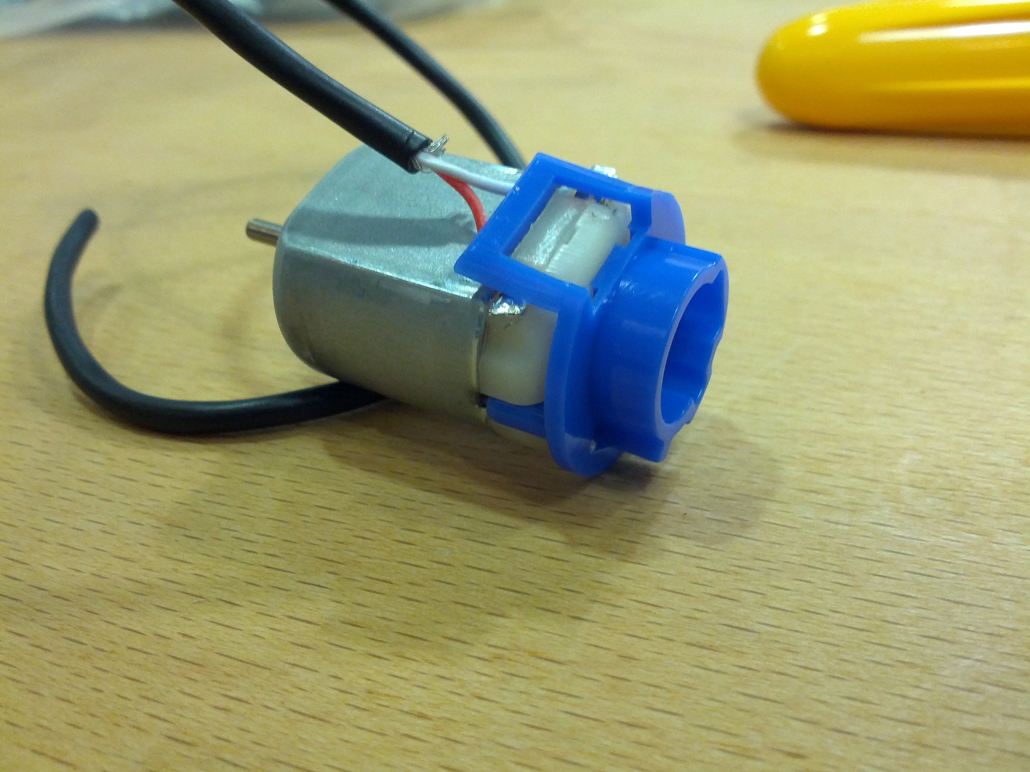
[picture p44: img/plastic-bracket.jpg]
plastic bracket
	

- Add **grease** to the motor shaft

- Add **the black rubber seal** onto the shaft

- Fold the cable over

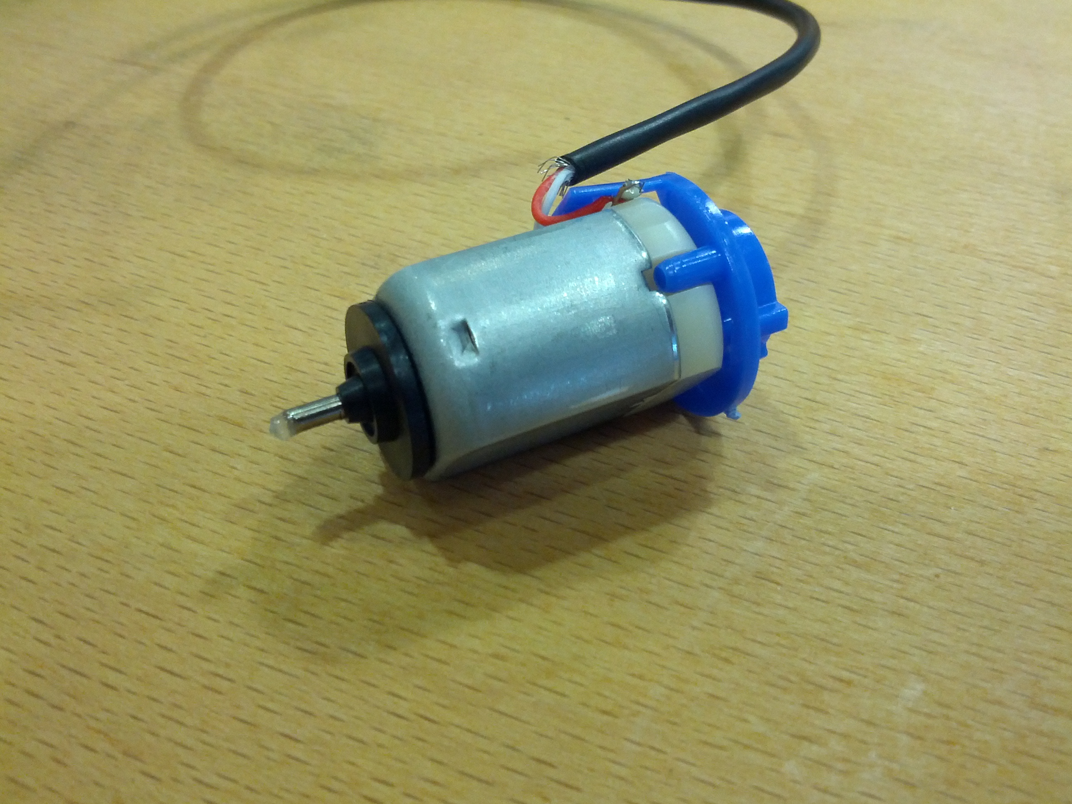
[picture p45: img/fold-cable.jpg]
fold-cable
	

- Insert motor in the propeller

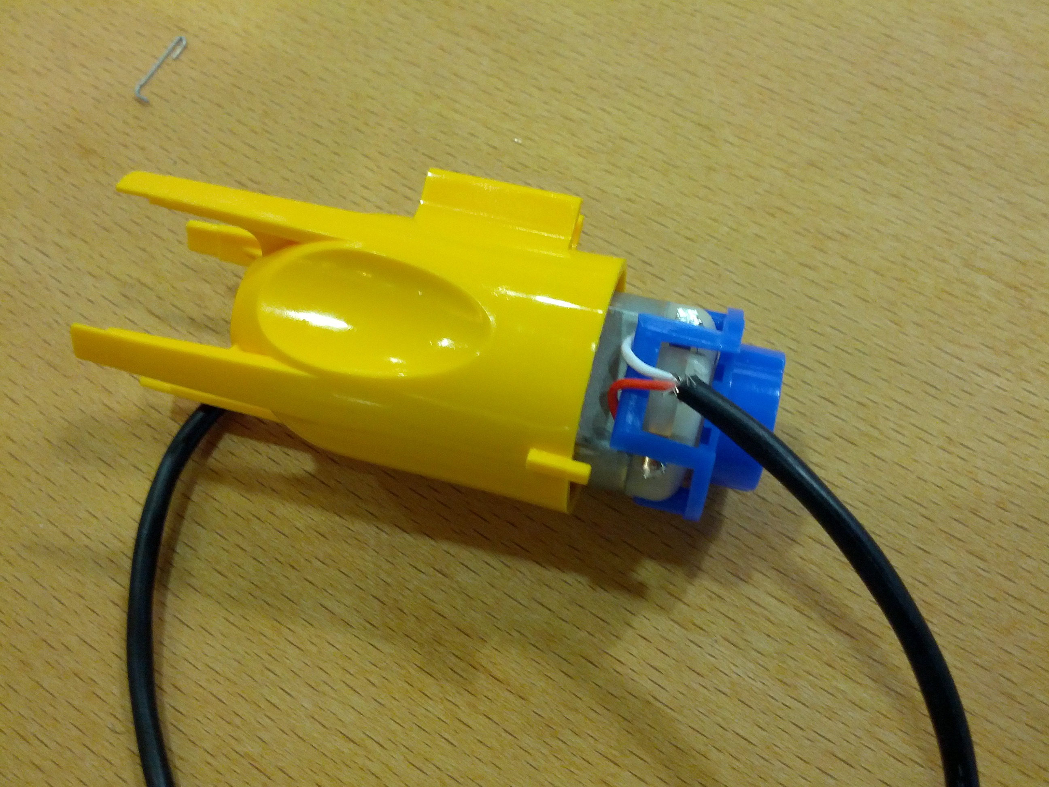
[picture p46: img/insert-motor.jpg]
insert cable
	

- Add the propeller blades

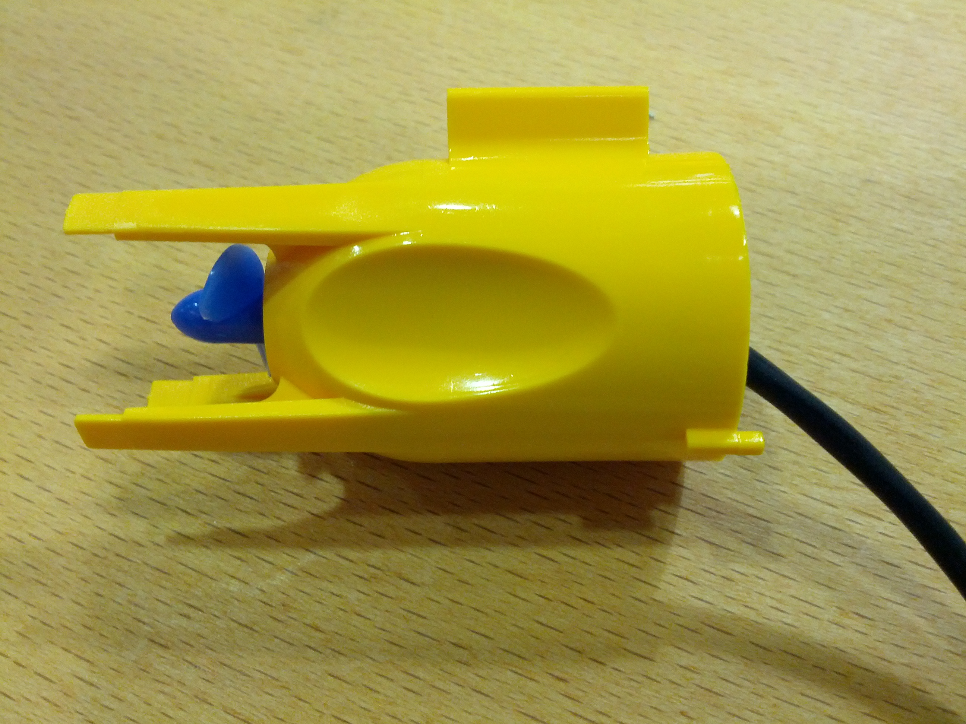
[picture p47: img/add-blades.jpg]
add blades
	

- Thread the wire through the hole in the front half of propeller

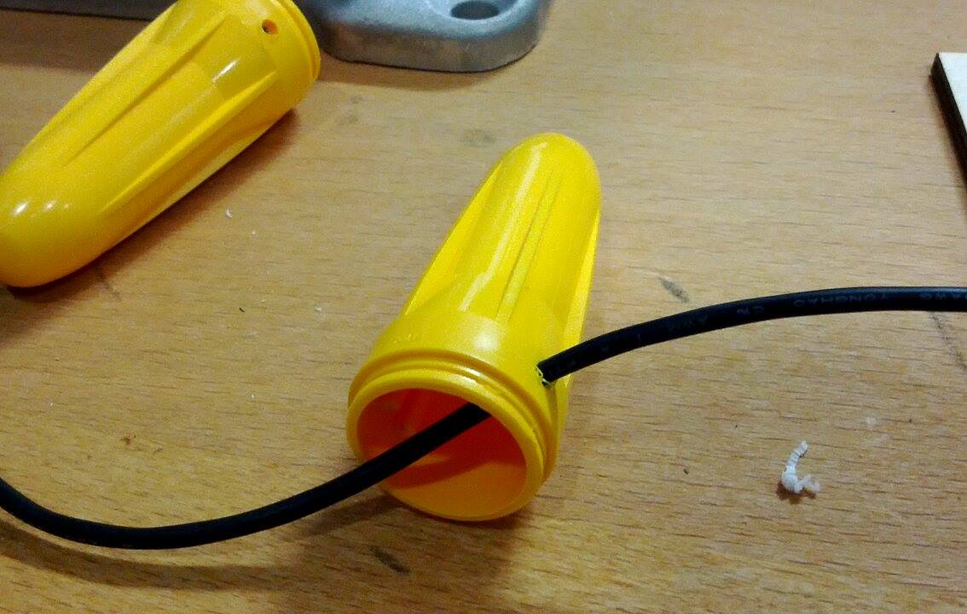
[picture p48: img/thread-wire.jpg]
thread wire
	

- Attach the two halves of the propeller

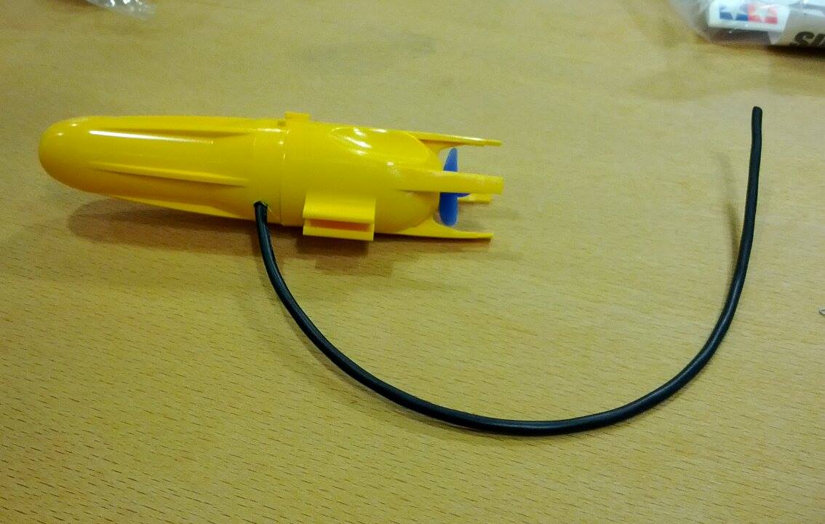
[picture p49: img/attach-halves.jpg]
attach halves
	

- Fill the wire hole with some silicone sealent.

## Add the Propeller!

1.  Now, replace the LEDs with motors (Tamiya Propellers)! And run the same above code. _VVvvvrrroooommmm vvrrrroooommm ;-)_

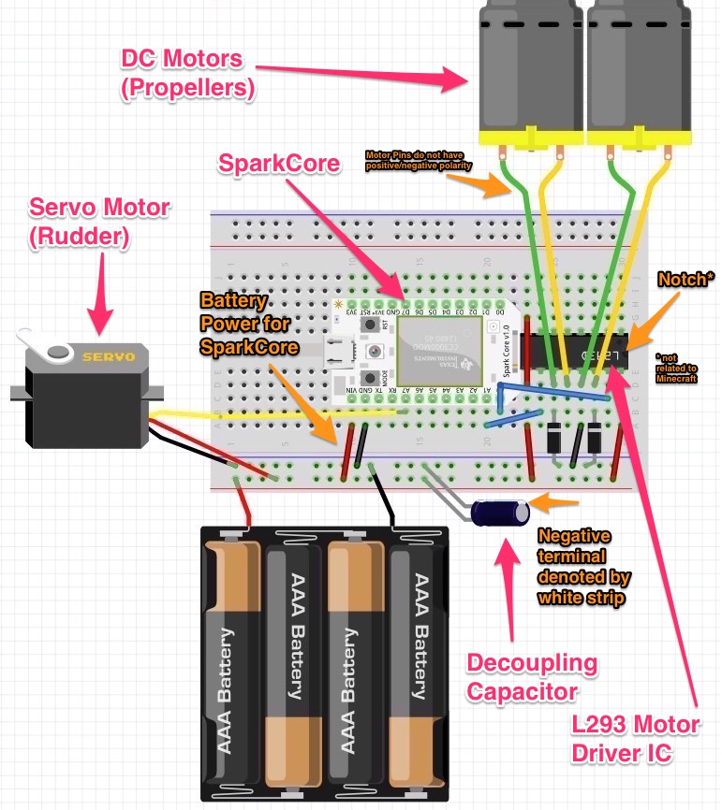
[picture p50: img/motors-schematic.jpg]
Motor Controller with Motors
	

	The original files for these schematic (made in [Fritzing](http://fritzing.org/download/)) are [here](https://github.com/notthetup/nodeboatbuilder/tree/master/schematics).

- Here are the connections for the updated schematic.

	| Signal           | Source                    | Destination  			       |
	|------------------|---------------------------|---------------------------|
	| Power(VCC)       | Battery Pack Red          | Power Rail on Breadboard  |
	| Ground(Gnd)      | Battery Pack Black        | Ground Rail on Breadboard |
	| Power(VCC)       | Vin on SparkCore          | Power Rail on Breadboard  |
	| Power(VCC)       | Pin 16 on L293D           | Power Rail on Breadboard  |
	| Power(VCC)       | Pin 8 on L293D            | Power Rail on Breadboard  |
	| Ground(Gnd)      | Gnd on SparkCore          | Ground Rail on Breadboard |
	| Ground(Gnd)      | Pin 12 on L293D           | Ground Rail on Breadboard |
	| Enable Motor     | Pin 9 on L293D            | Power Rail on Breadboard  |
	| Motor 1 Control  | Pin A0 on SparkCore       | Pin 15 on L293D           |
	| Motor 2 Control  | Pin A1 on SparkCore       | Pin 10 on L293D           |
	| _Motor 1 Pin 1_  | Pin 11 on L293D           | LED 1 Positive            |
	| _Motor 1 Pin 2_  | Pin 12 on L293D           | LED 1 Negative (shorter)  |
	| _Motor 2 Pin 1_  | Pin 14 on L293D           | LED 2 Positive            |
	| _Motor 1 Pin 2_  | Pin 13 on L293D           | LED 2 Negative (shorter)  |
	| Diode            | Ground Rail on Breadboard | Pin 11 on l293d           |
	| Diode            | Ground Rail on Breadboard | Pin 14 on L293D           |

- This method of connecting the motor allows us to either turn the motor on or off. You can't control the direction of the motor. If you accidently wired the motor such that it runs backwards then just swap the two pins that connect to the motor.

##Step 3: Add on the servo

A normal motor (DC Motor) that our propellers have allows us to move forward (and maybe backwards), but to change directions, we might need to use a Servo motor. Servos are precision motors that you can turn exact number of degrees from the center.

Servos are great for turning things accurately. In our scenario, we could turn propellers, rudders, fans, etc.

1. Follow the schematic below and add on the servo.

	Motor Controller with Servo

- Here are the connections for connecting the servo.

	|Signal           | Source                    | Destination  			       |
	|------------------|---------------------------|---------------------------|
	| Power(VCC)       | Battery Pack Red          | Power Rail on Breadboard  |
	| Ground(Gnd)      | Battery Pack Black        | Ground Rail on Breadboard |
	| Power(VCC)       | Orange on Servo           | Power Rail on Breadboard  |
	| Ground(VCC)      | Brown on Servo            | Ground Rail on Breadboard |
	| Servo Control    | Yellow on Servo           | Pin A7 on SparkCore |

	The original files for these schematic (made in [Fritzing](http://fritzing.org/download/)) are [here](https://github.com/notthetup/nodeboatbuilder/tree/master/schematics).
- Create a file `servo.js` with the following code:

	```js
	var five = require("johnny-five");
	var Spark = require("spark-io");

	var board = new five.Board({
	  io: new Spark({
	    token: process.env.SPARK_TOKEN,
	    deviceId: process.env.SPARK_DEVICE_ID
	  })
	});

	board.on("ready", function() {
	  var servo = new five.Servo("A7");

	  board.repl.inject({
	    s: servo
	  });

	});
	```

	Run this code with `node servo.js` - yes the servo should move!

	```js
	>> s.min() // set the servo to the minimum degrees, default to 0
	>> s.max() // set the servo to the maximum degrees, default to 180
	>> s.to(90) // move the servo to move the servo to degree 90
	```
- play with other [servo functions from Johnny Five](https://github.com/rwaldron/johnny-five/blob/master/docs/servo.md)
- Onwards to making the boat now. _Yiiiihooooo ;-)_

#Chapter 3 - Lets make Boat!

Now that we know how to control physical functionality, let's get creative and make a boat. Our boats needs to stay afloat, and it needs to move based on our control.

## Buoyancy

1. Buoyancy is critical in making boats. You don't want your boat to sink!
- Ensure that no water EVER! comes in contact with the electronics. Water and electronics don't mix.
- If your boat is heavy and has large portions of it under water, then you're adding drag to the boat. This is going to slow your boat down.
- You can always make your boat more boyant by attaching some styrofoam or plastic bottles to it.
- Ensure that there are no leaks in the boat, always pot all holes you drill with the silicone sealent. _No one ever liked leaky abstractions or boats._
- Keep in mind where you put your weights (motors, battries, SparkCore, etc). A level boat is more controllable than a boat which is tilted. _Just like with fonts_

## Propulsion

1. A single motor (propeller) can only propel you forward. If you want to be able to turn, you will need more control.
- Rudders are commonly used in combination propellers to change directions of a boat.

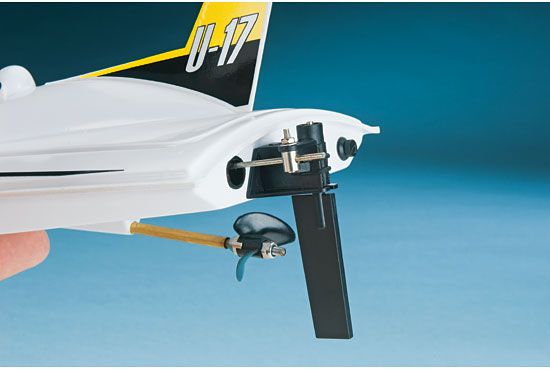
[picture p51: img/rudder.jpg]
	

- Rudders can made using servos and some acrylic.
- Here are some common propultion mechanism ideas.

	- 1 Propeller + 1 Servo controlling a Rudder (in the center)
	- 2 Propellers + 2 Servos controlling a Rudder (one on each side)
	- 1 Propeller attached to a Servo (in the center)
	- 2 Propellers attached to a Servo each (one on each side)
	- 2 Propellers using differential propultion

## Ideas

There are no correct answers to how you can design your boat, and it's propultion. Be creative, try stuff out, scour the interwebs for ideas, and come up with something novel. Use any materials avilable (_you may beg, borrrow and 'steal' stuff you need_) to use make our boat float and make it move forward!

- Here are some pictures and ideas to start you off.

	- [RC bottle boat](http://www.stormthecastle.com/Things/bottle-boat/bottle-boat-2.htm)
	- [servo boat rudder](https://www.google.com.sg/search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)
	- [boat propeller rudder](https://www.google.com.sg/search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)

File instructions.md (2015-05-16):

# Instructions for NodeBoatBuilder Attendees

All hands hoay! Welcome t' t' NodeBoats Builder workshop. We'll be makin' some sea farin' vessels over the weekend! Let's find out whose vessle will find the booty and whose will scuttle! Hahaha! And when we're all done, head out to the sea for some grog.

## To Bring

1. Laptop + Charger (With Nodejs pre-installed)
2. Shorts/Swim wear (you might need to jump into the 'pool' to fetch your boat)
3. Decorations for your boat. Pirates, canons, stickers, sails, go crazy!
4. An idea for the chasis of your boat. We will provide you some material (plastic boxes. bottles, bits and pieces of wood and plastic), but you can bring in more things that you want to use for your boat.

## Teams

We'll be working in teams of two. If you couldn't find a Player2 at registration, then we can pair you up at the begining of the workshop.

## Workshop material

The workshop material is already avilable [in this Github repo](https://github.com/notthetup/nodeboatbuilder)

# See you at the workshop!

Raise the Jolly Roger and let's begin!

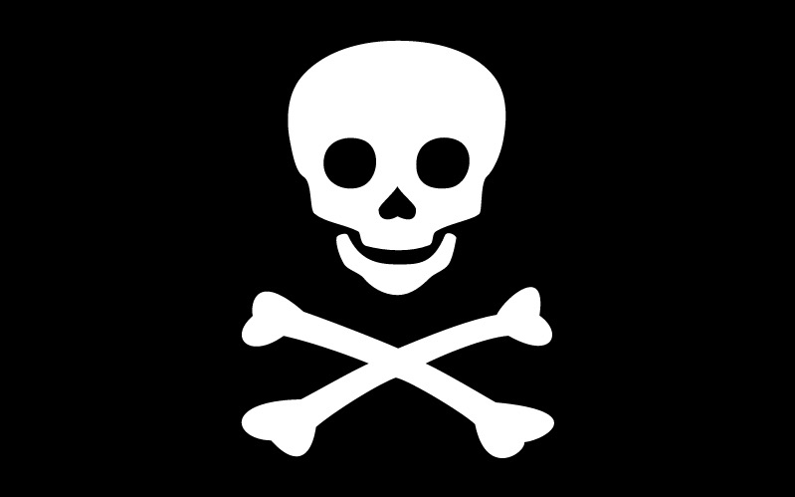
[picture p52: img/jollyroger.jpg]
Jolly Roger


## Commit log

2014-11-13 added fritzing drawring for motor control and notes
    [nodeboats.fzz]
2014-11-14 renamed schematic
    [motor.fzz]
2014-11-14 fixed motor schematic
    [bidirectional-motor.fzz, motor.fzz, servo.fzz]
2014-11-14 fixed bugs in schematic
    [bidirectional-motor.fzz, motor.fzz]
2014-11-14 added servo schematic
    [bidirectional-motor.fzz, motor.fzz, servo.fzz]
2014-11-15 added decoupling capacitors
    [bidirectional-motor.fzz, motor.fzz, servo.fzz]
2014-11-15 adjusted decoupling caps
    [bidirectional-motor.fzz, motor.fzz, servo.fzz]
2014-11-15 docs: components, motors and servo code
2014-11-16 added schematics
    [bidirectional-motor.fzz, motor.fzz, servo.fzz]
2014-11-16 added schematic images
    [motor-controller.fzz, motors.fzz]
2014-11-19 added connection table for motors
2014-11-19 updated servo connections table
2014-11-20 added propeller instructions
2014-11-22 updated schematic contoller
2014-11-24 updated schematics
    [bidirectional-motor.fzz, motor-controller.fzz, motors.fzz]
2014-11-24 tweaked pin orders
